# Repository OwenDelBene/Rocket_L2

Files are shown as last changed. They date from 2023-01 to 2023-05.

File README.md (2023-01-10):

# L2Rocket
Rocket flight software, simulations, and CAD for a high powered rocket preparing for a L2 certification. 

## Avionics

#### Arduino Uno:
Flight computer powered by 9V battery, armed with screw switch.

#### BMP085:
Barometric pressure sensor connected to Flight computer over I2C.

#### LSM6Ds3:
3 axis accelerometer and gyroscope connected to Flight computer over I2C.

## Structure
Plywood: fins, centering ring  
Cardboard: aft airframe,  motor tube  
PetG: Avionics bay, nosecone, forward airframe, motor retainer, rail buttons

## Software

#### State machine:
High powered rockets go through 4 states: ground idle, powered ascent, unpowered ascent, descent. 
    
- During ground idle both sensors are initialized and begin returning data. The Kalman filter is intiailized and begins filtering altitude and vertial acceleration returned from the barometric pressure sensor and accelerometer respectively to return position velocity and acceleration. Leds are lit to elucidate the state on the launch rail. The initial altitude is recorded for reference.  
- The rocket enters powered ascent when it has detected sufficient vertical acceleration and sufficient altitude relative to the initial altitude.   
- The rocket enters unpowered ascent when the vertical acceleration becomes negative. The ejection charge for the drogue parachute is fired when vertical velocity is zero. For safety the ejection charge can only be fired above a certain altitude.    
- The rocket enters descent when its velocity becomes negative and for safety above a certain altitude. During descent the ejection charge for the main parachute is fired at an 300m above initial altitude as determined by openrocket simulations. 

#### Kalman Filter:
Takes input altitude and acceleration data and outputs position velocity and acceleration. Utilizes measurement noise from sensor datasheets. 

## Simulations

#### Openrocket:
Openrocket was used to simulate the rocket design with various J class rocket motors to determine the appropirate altitude for main chute release, and determine rocket stability. 

## Testing
#### Ejection testing
An esp32 hosted a http server to remotely control the flight computer, sending signals to trigger the ejection charges to ensure sufficient pressure for separation.
#### Hardware in the loop:
Sensors were turned off and Kalman filter was fed altitude and acceleration data with noise from recorded thrust curves for various J class rocket motors. State transitions were recorded with the current input data as well as the state vector returned by the kalman filter, to verify flight software state machine.

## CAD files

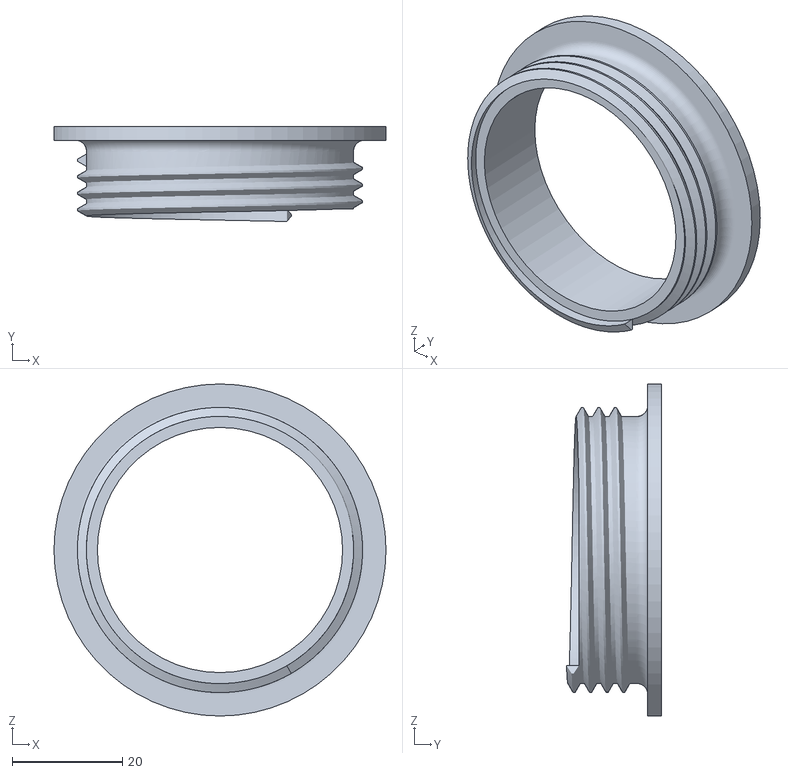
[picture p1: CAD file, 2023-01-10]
CAD/RetainerMale.STL
60.3 x 17.2 x 60.3

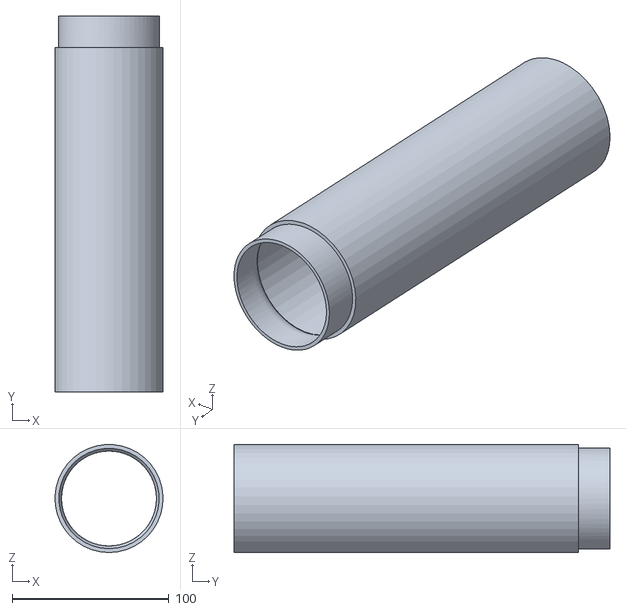
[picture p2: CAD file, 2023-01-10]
CAD/TopBodyExtension.STL
68.9 x 240.0 x 69.0

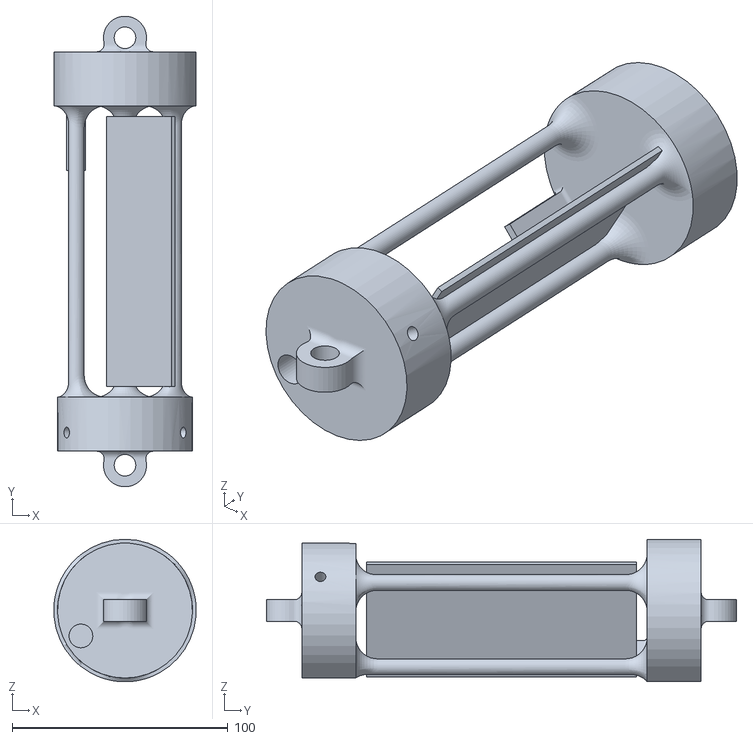
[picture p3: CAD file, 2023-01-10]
CAD/AvBay.STL
65.8 x 217.9 x 66.0

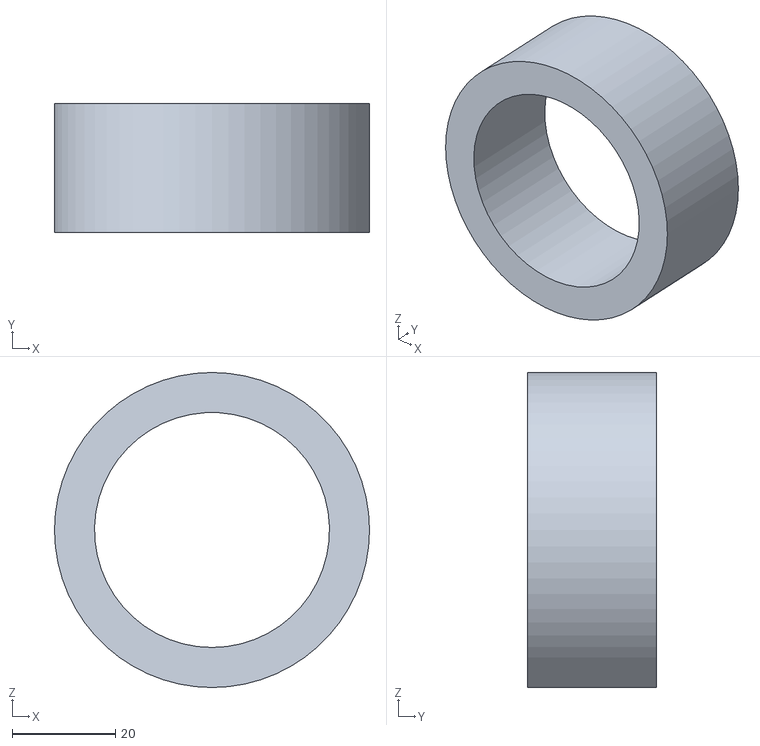
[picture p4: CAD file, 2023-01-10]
CAD/CenteringRing.STL
61.0 x 25.0 x 61.0

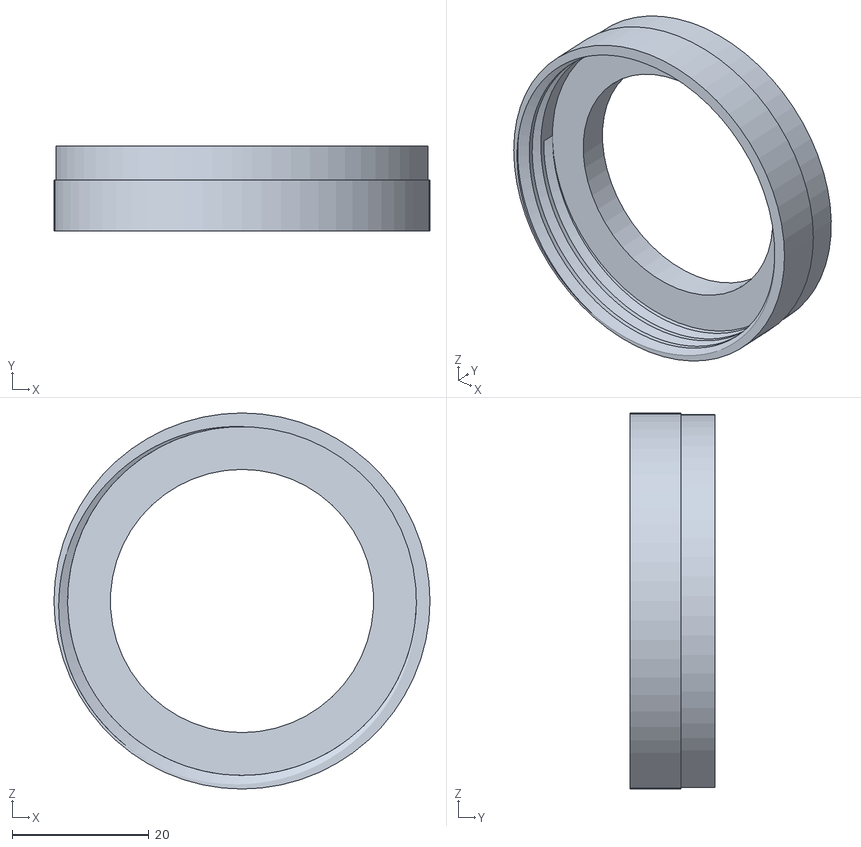
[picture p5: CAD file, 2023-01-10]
CAD/MotorRetainerFemale.STL
55.0 x 12.5 x 55.0

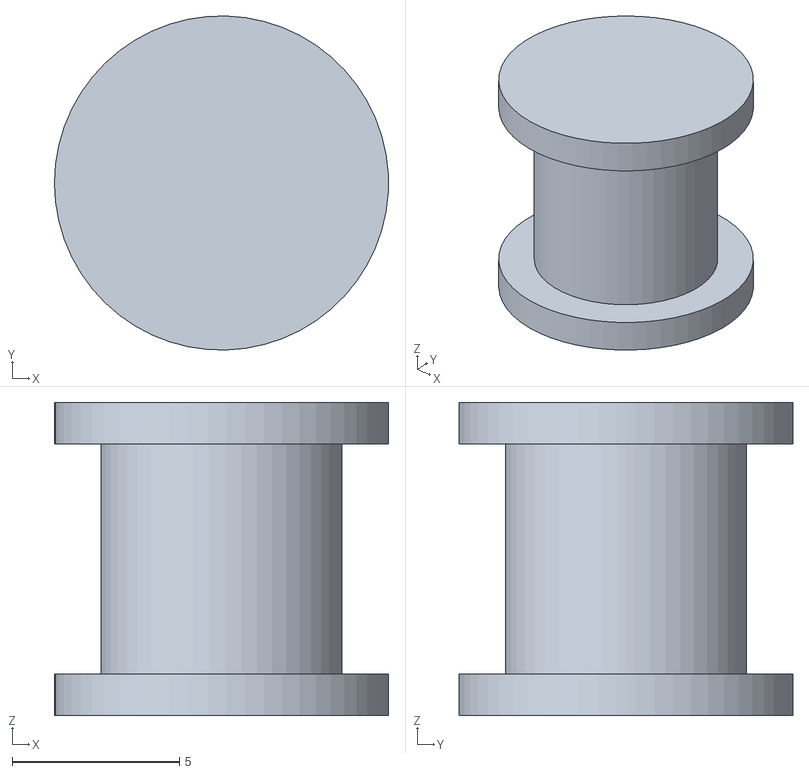
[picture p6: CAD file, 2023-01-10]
CAD/LaunchLug.STL
10.0 x 10.00 x 9.38

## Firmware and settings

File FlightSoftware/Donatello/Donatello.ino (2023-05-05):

//#include <avr/io.h>
//#include <util/delay.h>


#include <Wire.h> // Must include Wire library for I2C

#include "include/LSM6DS3.h"
#include "include/BMP180.h"
#include "include/State.h"







State state;





/*int main()
{
  
  //TODO standardize pinouts
  // DDRB |= (1<<5); // GroundIdle
  // DDRB |= (1<<4); // Ground success
  // DDRB |= (1<<2); // Deploy2
  // DDRB |= (1<<3); // Deploy1

  
  Serial.begin(9600);
  Serial.println("hi init");
  accel.init();
  Serial.println("hi accel");
  //_delay_ms(5000); //5 second delay to save data while ground idle
  State state;
  state.K_init();
  state.time = millis();
  while(1)
  {
    Serial.println("hi");
    //TODO investigate and standardize thresholds
    state.Update();
    Serial.println("hi2, \n");
    Serial.println(state.altitude) ; 
    Serial.println(state.velocity); 
    Serial.println(state.acceleration);
    Serial.println('\n');
    if (state.altitude < 50.0f && state.velocity < 5.0f) GroundIdle(state);

    if (state.velocity > 5.0f && state.acceleration > 2.0f && state.Ground) PoweredFlight(state);

    if (state.velocity > -1.0f && state.acceleration < -9.0f && state.altitude > 100.0f  && state.Powered) UnpoweredAscent(state);
    
    if (state.velocity < -5.0f && state.acceleration < 0.0f && state.Deploy1) UnpoweredDescent(state);

    if (state.velocity < 0.5f && state.acceleration < 0.1f && state.Deploy2) Landed(state);
    
    
    
  }

  return 0;
}*/



void setup()
{
  Serial.begin(115200);
//TODO standardize pinouts
  // DDRB |= (1<<5); // GroundIdle
  // DDRB |= (1<<4); // Ground success
  // DDRB |= (1<<2); // Deploy2
  // DDRB |= (1<<3); // Deploy1

  
  Serial.begin(9600);



  //_delay_ms(5000); //5 second delay to save data while ground idle
  
  state.K_init();
  state.time = millis();

}



void loop()
{
  Serial.println("hi");
    //TODO investigate and standardize thresholds
    state.Update();
    Serial.println("altitude, velocity, acceleration, \n");
    Serial.println(state.altitude) ; 
    Serial.println(state.velocity); 
    Serial.println(state.acceleration);
    Serial.println('\n');
    if (state.altitude < 50.0f && state.velocity < 5.0f) GroundIdle(state);

    if (state.velocity > 5.0f && state.acceleration > 2.0f && state.Ground) PoweredFlight(state);

    if (state.velocity > -1.0f && state.acceleration < -9.0f && state.altitude > 100.0f  && state.Powered) UnpoweredAscent(state);
    
    if (state.velocity < -5.0f && state.acceleration < 0.0f && state.Deploy1) UnpoweredDescent(state);

    if (state.velocity < 0.5f && state.acceleration < 0.1f && state.Deploy2) Landed(state);

}

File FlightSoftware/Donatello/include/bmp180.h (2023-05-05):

//3.6V max
//SCL 3.4MHz
//Need pullup resistor 4.7kOhm
#include "I2C.h"


#ifndef BMP180_H
#define BMP180_H



#define BMP180_CALIB_DATA_SIZE        (22)
#define BMP180_calibration_params_AC1_MSB    (0)
#define BMP180_calibration_params_AC1_LSB    (1)
#define BMP180_calibration_params_AC2_MSB    (2)
#define BMP180_calibration_params_AC2_LSB    (3)
#define BMP180_calibration_params_AC3_MSB    (4)
#define BMP180_calibration_params_AC3_LSB    (5)
#define BMP180_calibration_params_AC4_MSB    (6)
#define BMP180_calibration_params_AC4_LSB    (7)
#define BMP180_calibration_params_AC5_MSB    (8)
#define BMP180_calibration_params_AC5_LSB    (9)
#define BMP180_calibration_params_AC6_MSB    (10)
#define BMP180_calibration_params_AC6_LSB    (11)
#define BMP180_calibration_params_B1_MSB     (12)
#define BMP180_calibration_params_B1_LSB     (13)
#define BMP180_calibration_params_B2_MSB     (14)
#define BMP180_calibration_params_B2_LSB     (15)
#define BMP180_calibration_params_MB_MSB     (16)
#define BMP180_calibration_params_MB_LSB     (17)
#define BMP180_calibration_params_MC_MSB     (18)
#define BMP180_calibration_params_MC_LSB     (19)
#define BMP180_calibration_params_MD_MSB     (20)
#define BMP180_calibration_params_MD_LSB     (21)


#define BMP180_SLAVE_ADDR (0xEE >> 1)
#define BMP180_OUT_XLSP 0xF8
#define BMP180_OUT_LSP 0xF7
#define BMP180_OUT_MSP 0xF6
#define BMP180_CTRL_MEASUREMENT_REG 0xF4
#define BMP180_RESET 0xE0
#define BMP180_CHIP_ID_REG 0xD0
#define BMP180_TEMPERATURE_CTRL 0x2E
#define BMP180_PRESSURE_CTRL 0xF4 //output sampling rate 3 for lower output sampling rate 0xB4, 0x74, and 0x34 for the lowest
#define BMP180_EEPROM_START_ADDR 0xAA
#define BMP180_EEPROM_DATA_LEN 22
#define BMP180_VERSION_REG 0xD1




#define BMP180_GET_BITSLICE(regvar, bitname) \
    ((regvar & bitname##__MSK) >> (bitname##__POS))
#define BMP180_SET_BITSLICE(regvar, bitname, val) \
    ((regvar & ~bitname##__MSK) | ((val << bitname##__POS) & bitname##__MSK))
#define BMP180_CHIP_ID__POS (0)
#define BMP180_CHIP_ID__MSK (0xFF)
#define BMP180_CHIP_ID__LEN (8)
#define BMP180_CHIP_ID__REG (BMP180_CHIP_ID_REG)

#define BMP180_ML_VERSION__POS (0)
#define BMP180_ML_VERSION__LEN (4)
#define BMP180_ML_VERSION__MSK (0x0F)
#define BMP180_ML_VERSION__REG (BMP180_VERSION_REG)

#define BMP180_AL_VERSION__POS (4)
#define BMP180_AL_VERSION__LEN (4)
#define BMP180_AL_VERSION__MSK (0xF0)
#define BMP180_AL_VERSION__REG (BMP180_VERSION_REG)


#define BMP180_ERROR 255

/**
 * @brief Container for calibration parameters
 * 
 */
struct BMP180_calibration
{
    uint16_t ac1;
    uint16_t ac2;
    uint16_t ac3;
    uint16_t ac4;
    uint16_t ac5;
    uint16_t ac6;
    uint16_t b1;
    uint16_t b2;
    uint16_t mb;
    uint16_t mc;
    uint16_t md;
};

struct BMP180
{
    struct BMP180_calibration calibration_params;
    uint8_t mode; //power mode
    uint8_t chip_id; //used for testing
    uint8_t device_addr; 
    uint8_t slave_addr = BMP180_SLAVE_ADDR;
    
    uint8_t ml_version; /**<ml version*/
    uint8_t al_version; /**<al version*/

    uint8_t sensortype; /**< sensor type*/
    int32_t param_b5; /**<pram*/
    int32_t number_of_samples; /**<sample calculation*/
    int16_t oversamp_setting; /**<oversampling setting*/
    int16_t sw_oversamp; /**<software oversampling*/


    uint8_t oss;


    double Pressure0 = 1013.25; //hPa 






    /**
     * @brief Computes B5 calibration parameter, taken from datasheet
     * 
     * @param calCoeff Calibration coefficient struct
     * @param ut uncalibrated temperature
     * @return int32_t B5 calibration parameter
     */
    int32_t computeB5(BMP180_calibration* calCoeff ,int32_t ut)
    {
        int32_t x1 = (((ut - (int32_t)calCoeff->ac6) * (int32_t)calCoeff->ac5) >> 15 );
        int32_t x2= ((int32_t)calCoeff->mc << 11) / (x1 + (int32_t)calCoeff->md);
        return x1+x2;
    }

    /**
     * @brief Populate the calibration Parameter structure
     * 
     */
    void getCalibrationParameters()
    {

        
        //Check chip ID to make sure

        uint8_t calibData[BMP180_EEPROM_DATA_LEN];
        readBytes(this->slave_addr,BMP180_EEPROM_START_ADDR, calibData, BMP180_EEPROM_DATA_LEN );

        this->calibration_params.ac1 =(int16_t)((((int32_t)((int8_t)calibData[BMP180_calibration_params_AC1_MSB])) << 8) |
                calibData[BMP180_calibration_params_AC1_LSB]);

        this->calibration_params.ac2 =
            (int16_t)((((int32_t)((int8_t)calibData[BMP180_calibration_params_AC2_MSB])) << 8) |
                calibData[BMP180_calibration_params_AC2_LSB]);
        this->calibration_params.ac3 =
            (int16_t)((((int32_t)((int8_t)calibData[BMP180_calibration_params_AC3_MSB])) << 8) |
                calibData[BMP180_calibration_params_AC3_LSB]);
        this->calibration_params.ac4 =
            (uint16_t)((((uint32_t)((uint8_t)calibData[BMP180_calibration_params_AC4_MSB])) << 8) |
                calibData[BMP180_calibration_params_AC4_LSB]);
        this->calibration_params.ac5 =
            (uint16_t)((((uint32_t)((uint8_t)calibData[BMP180_calibration_params_AC5_MSB])) << 8) |
                calibData[BMP180_calibration_params_AC5_LSB]);
        this->calibration_params.ac6 =
            (uint16_t)((((uint32_t)((uint8_t)calibData[BMP180_calibration_params_AC6_MSB])) << 8) |
                calibData[BMP180_calibration_params_AC6_LSB]);

        /*parameters B1,B2*/
        this->calibration_params.b1 =
            (int16_t)((((int32_t)((int8_t)calibData[BMP180_calibration_params_B1_MSB])) << 8) |
                calibData[BMP180_calibration_params_B1_LSB]);
        this->calibration_params.b2 =
            (int16_t)((((int32_t)((int8_t)calibData[BMP180_calibration_params_B2_MSB])) << 8) |
                calibData[BMP180_calibration_params_B2_LSB]);

        /*parameters MB,MC,MD*/
        this->calibration_params.mb =
            (int16_t)((((int32_t)((int8_t)calibData[BMP180_calibration_params_MB_MSB])) << 8) |
                calibData[BMP180_calibration_params_MB_LSB]);
        this->calibration_params.mc =
            (int16_t)((((int32_t)((int8_t)calibData[BMP180_calibration_params_MC_MSB])) << 8) |
                calibData[BMP180_calibration_params_MC_LSB]);
        this->calibration_params.md =
            (int16_t)((((int32_t)((int8_t)calibData[BMP180_calibration_params_MD_MSB])) << 8) |
                calibData[BMP180_calibration_params_MD_LSB]);
    }

    /**
     * @brief Initialize sensor structure
     * 
     */
    void Init()
    {
        
        uint8_t deviceInfo = 0;
        Serial.print("reading bytes from slave addr: ");
        readBytes(this->slave_addr, BMP180_CHIP_ID_REG, &deviceInfo, 1);
        this->chip_id =BMP180_GET_BITSLICE(deviceInfo, BMP180_CHIP_ID);

        this->number_of_samples = 1;
        this->oversamp_setting = 0;
        this->sw_oversamp = 0;

        readBytes(this->slave_addr, BMP180_VERSION_REG,&deviceInfo, 1 );
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
